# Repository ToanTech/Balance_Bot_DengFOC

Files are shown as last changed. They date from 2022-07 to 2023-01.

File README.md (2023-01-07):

**DengFOC平衡车项目**是基于simplefoc开源的[平衡车项目](https://github.com/simplefoc/Arduino-FOC-balancer)，进行结构改进和效果优化后应用在我开源的[DengFOC](https://gitee.com/link?target=https%3A%2F%2Fgithub.com%2FToanTech%2FDeng-s-foc-controller)双路无刷电机驱动器上的DengFOC配套项目。

balancebot_gif

get_down

**项目完全开源，你可以根据本Github内容自行白嫖，或者，支持一下灯哥的辛勤劳作，进入灯哥开源TB店购买DengFOC平衡车套件，一键配齐。**

[DengFOC 高敏捷自平衡车套件--链接猛击(进店后在 所有宝贝 处可找到)](https://shop564514875.taobao.com/)

# 一、安装过程
## 1.所需元器件

1. DengsFOC V3（你可以在TB搜索灯哥开源进入店铺购买，或根据DengFOC开源仓库的开源资料自制）
1. 2204云台电机*2
1. AS5600编码器*2
1. MPU6050陀螺仪*1
## 2.接线过程
| 零件 | 接线位置 |
| --- | --- |
| 2204云台电机 | DengFoc M0位置 |
| 2204云台电机 | DengFoc M1位置 |
| AS5600 | SDA0,SCL0,3V3,GND |
| AS5600 | SDA1,SCL1,3V3,GND |
| MPU6050 | SDA1,SCL1,3V3,GND |
| 电池以及电源开关线 | DengFoc 电源端子 |

<div align=center>&width=540"</div>
如果你是自行DIY，那么按照上面的接线表格将线接入DengFOC即可；如果你是采用在 [灯哥开源 淘宝店](https://gitee.com/link?target=https%3A%2F%2Fshop564514875.taobao.com%2F) 购买的平衡车套件，那么你会得到**如下所示配套线材**。
配套接线材料：

- AS5600编码器接线套装 一头是杜邦端子，接有一根黑线GND，一根红线VCC，一根绿线SDA，一根黄线SCL，另一端是4p端子。

<div align=center>&width=324"</div>

- MPU6050接线端子套装  两头是4p端子，接有一根黑线GND，一根红线VCC，一根绿线SDA，一根黄线SCL。

<div align=center>&width=217"
</div>

- 电源接线开关
## 3.组装步骤

- AS5600编码器红色线代表VCC，黑色线代表GND，黄线代表SCL，绿色代表SDA。将端子一端的4p端子连接到AS5600对应的端子上。同时将接线端子的另外一端杜邦壳接到DengFoc的排针对应的接口上。

<div align=center>&width=1024"</div>

- MPU6050陀螺仪接线端子红色线代表VCC，黑色线代表GND，黄色线代表SCL，绿色线代表SDA，接线端子一端MPU6050连接，一端与AS5600编码器相连。

<div align=center>&width=1156"</div>

- 电机1三线连接到DengFoc M0端旋转方向为cw，电机2连接到DengFoc M1端旋转方向为ccw。可通过串口查看旋转方向信息，若旋转方向不对可更换电机三相中任意两相顺序。

详细安装过程可以观看安装视频，视频中有关于车体各部分的详细安装步骤以及连线步骤。
<div align=center>&width=951"</div>
# 二、调试过程

- 烧写平衡车代码例程，上电之后等待陀螺仪校准，以及电机校准。
- 看平衡车是否能够自稳。
- 微信扫描下图二维码，进入小程序。

<div align=center>&width=206.4"</div>

- 进入小程序页面，看蓝牙是否连接成功。小程序页面图如下所示。

<div align=center>&width=320"</div>

- 接着移动摇杆看功能是否正常。
- 如果想自己DIY小车控制速度，可以在例程中对小车控制参数进行修改。

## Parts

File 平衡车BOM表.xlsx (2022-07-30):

电控 |  |  | 机械
零件名称 | 数量 | 备注 | 零件名称 | 数量
DengFOC | 1 |  | 车身主体打印件1 | 1
MPU6050 | 1 |  | 车轮打印件 | 2
AS5600 | 2 |  | 车身前盖打印件 | 1
配套传感器径向磁铁 | 2 |  | 车轮轴体打印件2 | 2
2204云台电机 | 2 |  | 编码器支架 | 2
MPU6050 4p端子线 | 2 |  | M2.5*4螺丝 | 8
AS5600 4p端子线 | 2 | 电机TB地址：https://item.taobao.com/item.htm?id=647180650088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 | M3x10螺丝 | 26
3S电池 | 1 |  | M3螺母 | 2

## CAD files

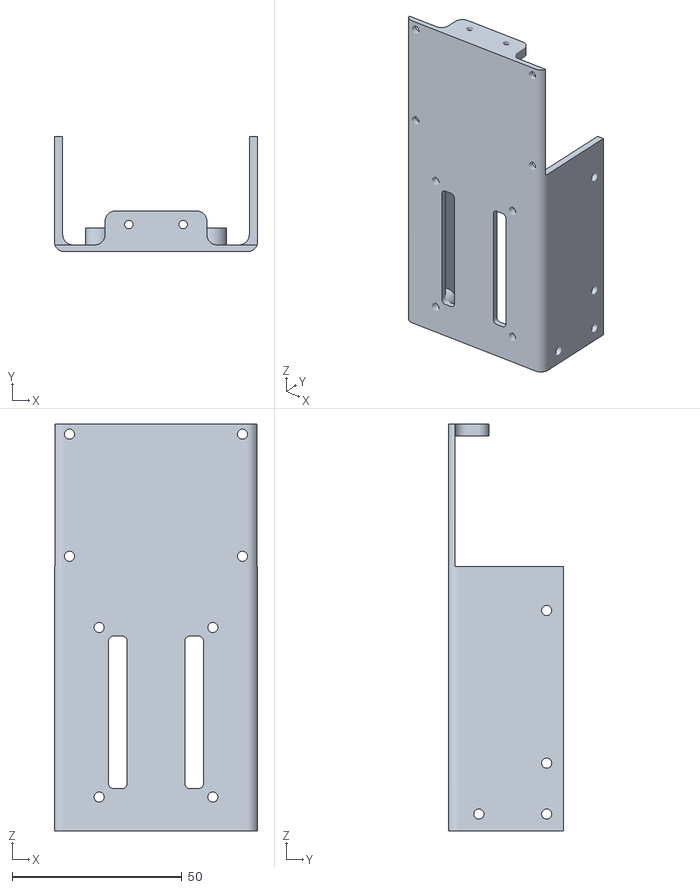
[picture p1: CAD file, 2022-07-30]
平衡车3D打印件/body_21.stl
60.0 x 34.0 x 120.0

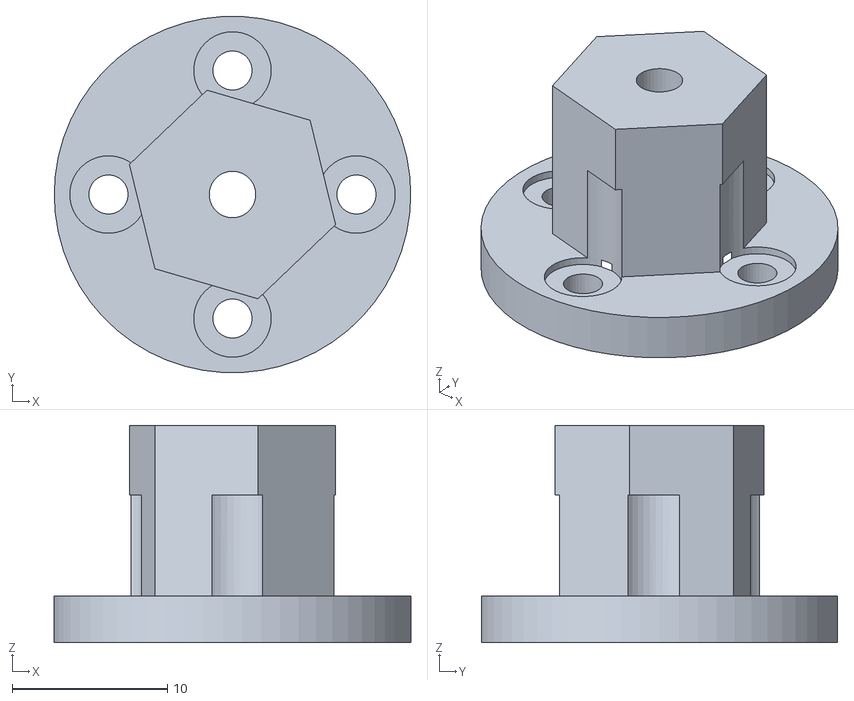
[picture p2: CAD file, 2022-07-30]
平衡车3D打印件/tire_motor_binderx2.STL
23.0 x 23.0 x 14.0

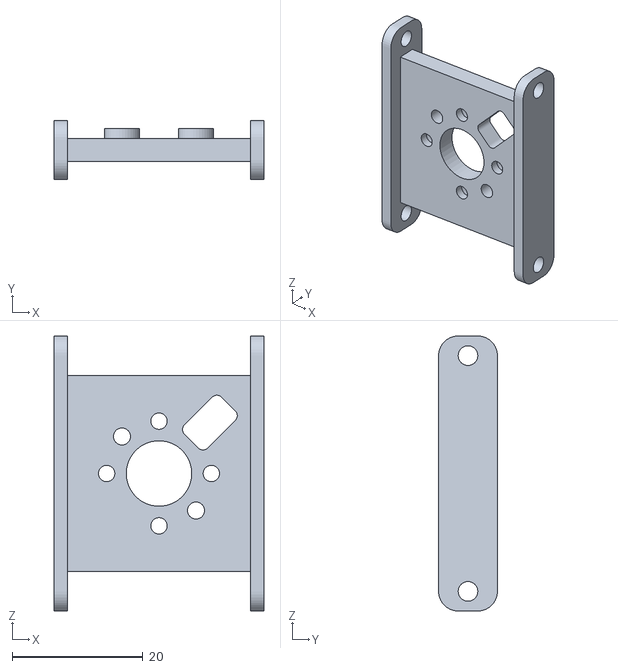
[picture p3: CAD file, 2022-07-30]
平衡车3D打印件/new_car_codex2.STL
32.0 x 9.00 x 42.0

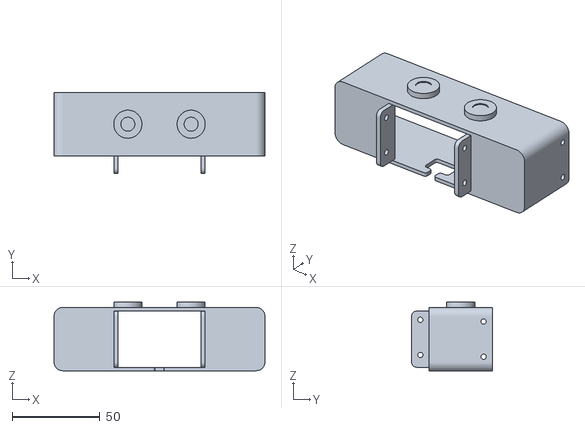
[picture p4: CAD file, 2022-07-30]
平衡车3D打印件/head_19.stl
120.0 x 46.0 x 39.0

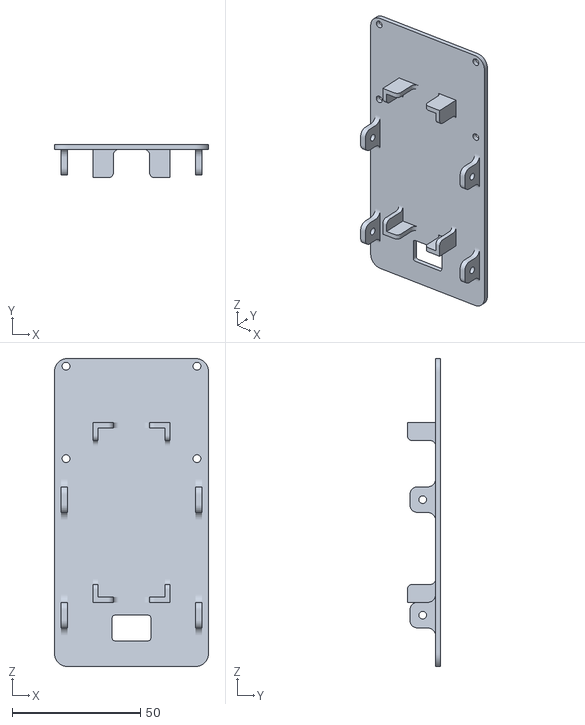
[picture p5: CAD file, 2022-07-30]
平衡车3D打印件/body_cover_with_bat.stl
60.0 x 13.0 x 120.0

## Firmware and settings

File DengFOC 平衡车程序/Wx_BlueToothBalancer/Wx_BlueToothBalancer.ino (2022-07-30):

// 更换蓝牙库
#include <Arduino.h>
#include <SimpleFOC.h>
#include <MPU6050_tockn.h>
#include <BLEDevice.h>
#include <BLEServer.h>
#include <BLEUtils.h>
#include <BLE2902.h>

#define gyroY_OFF -0.56

// 蓝牙参数
BLEServer *pServer = NULL;
BLECharacteristic * pTxCharacteristic;
bool deviceConnected = false;
bool oldDeviceConnected = false;
uint8_t txValue = 0;

#define SERVICE_UUID           "6E400001-B5A3-F393-E0A9-E50E24DCCA9E" // UART service UUID
#define CHARACTERISTIC_UUID_RX "6E400002-B5A3-F393-E0A9-E50E24DCCA9E"
#define CHARACTERISTIC_UUID_TX "6E400003-B5A3-F393-E0A9-E50E24DCCA9E"

TwoWire I2Cone = TwoWire(0);
TwoWire I2Ctwo = TwoWire(1);
MagneticSensorI2C sensor0 = MagneticSensorI2C(AS5600_I2C);
MagneticSensorI2C sensor1 = MagneticSensorI2C(AS5600_I2C);


double acc2rotation(double x, double z);//for kalman
MPU6050 mpu6050(I2Ctwo);


BLDCMotor motor0 = BLDCMotor(7);
BLDCDriver3PWM driver0 = BLDCDriver3PWM(32,33,25,22);

BLDCMotor motor1 = BLDCMotor(7);
BLDCDriver3PWM driver1  = BLDCDriver3PWM(26,27,14,12);

// control algorithm parametersw
// stabilisation pid 自稳PID
//P0.55 I5.5 初始值0.5 5 
PIDController pid_stb{.P = 0.8, .I = 5.5, .D = 0, .ramp = 100000, .limit = 8}; 
// velocity pid 速度PID P初始值1.5
PIDController pid_vel{.P = 1.5, .I = 0, .D = 0.01, .ramp = 10000, .limit = _PI/4};
// velocity control filtering 速度控制滤波，滤波时间常数为0.07
LowPassFilter lpf_pitch_cmd{.Tf = 0.07};
// low pass filters for user commands - throttle and steering 油门和转向滤波
LowPassFilter lpf_throttle{.Tf = 0.5}; //初始值0.5
LowPassFilter lpf_steering{.Tf = 0.1};//初始值0.1

String resStr;
String chipId;
String readString;

float steering = 0;
float throttle = 0;
float new_steering;
float new_throttle;
// max_throttle数值可能需要更改
float max_throttle = 50; // 初始值20 rad/s 
float max_steering = 0.8; //  1V
float Offset_parameters = -9.3; //偏置参数
int Checkcomma; //判断是否含有逗号分隔


Commander commander = Commander(Serial);
void cntStab(char* cmd) {  commander.pid(&pid_stb, cmd);}
void cntMove(char* cmd) {  commander.pid(&pid_vel, cmd);}
void lpfPitch(char* cmd) {  commander.lpf(&lpf_pitch_cmd, cmd);}
void lpfSteering(char* cmd) {  commander.lpf(&lpf_steering, cmd);}
void lpfThrottle(char* cmd) {  commander.lpf(&lpf_throttle, cmd);}

class MyServerCallbacks: public BLEServerCallbacks {
    void onConnect(BLEServer* pServer) {
      deviceConnected = true;
    };

    void onDisconnect(BLEServer* pServer) {
      deviceConnected = false;
    }
};



class MyCallbacks: public BLECharacteristicCallbacks {
    void onWrite(BLECharacteristic *pCharacteristic) {
      std::string rxValue = pCharacteristic->getValue();

      if (rxValue.length() > 0) {
        Serial.print("Received Value: ");
        // 打印蓝牙接收信息
        for (int i = 0; i < rxValue.length(); i++){
//          Serial.print(rxValue[i]);
          resStr += rxValue[i];
        }
        Checkcomma = resStr.indexOf(',');
        if(Checkcomma != -1){
          new_steering = resStr.substring(0,Checkcomma).toInt();
          new_throttle = resStr.substring(Checkcomma+1,resStr.length()).toInt();
          steering = max_steering * new_steering/50;
          throttle = max_throttle * -new_throttle/50;
//          Serial.print("new_steering:");
//          Serial.print(new_steering);
//          Serial.print("\t");
//          Serial.print("new_throttle:");
//          Serial.print(new_throttle);
//          Serial.print("Y:");
//          Serial.print(throttle);
//          Serial.print("\t");
//          Serial.print("X:");
//          Serial.println(steering);
        }
        else{
          steering = 0;
          throttle = 0;
        }
        // 清空数据准备下次接收
        resStr = "";
      }
    }
};

void setup(){
    Serial.begin(115200);
    _delay(750);

    chipId = String((uint32_t)ESP.getEfuseMac(), HEX);
    chipId.toUpperCase();
    Serial.println(chipId);
    //  初始化蓝牙 蓝牙名称
    BLEDevice::init("Blue Control");

    // 开启一个蓝牙服务
    pServer = BLEDevice::createServer();
    pServer->setCallbacks(new MyServerCallbacks());

    BLEService *pService = pServer->createService(SERVICE_UUID);

    pTxCharacteristic = pService->createCharacteristic(
                        CHARACTERISTIC_UUID_TX,
                        BLECharacteristic::PROPERTY_NOTIFY
                      );

    pTxCharacteristic->addDescriptor(new BLE2902());

    BLECharacteristic * pRxCharacteristic = pService->createCharacteristic(
        CHARACTERISTIC_UUID_RX,
        BLECharacteristic::PROPERTY_WRITE
                                          );

    pRxCharacteristic->setCallbacks(new MyCallbacks());

    pService->start();

    pServer->getAdvertising()->start();
    Serial.println("Waiting a client connection to notify...");

    I2Cone.begin(19,18, 400000UL); 
    I2Ctwo.begin(23,5, 400000UL);
  
    sensor0.init(&I2Cone);
    sensor1.init(&I2Ctwo);

    mpu6050.begin();
    mpu6050.calcGyroOffsets(true);

    // link the motor to the sensor
    motor0.linkSensor(&sensor0);
    motor1.linkSensor(&sensor1);

     // 速度环PID参数
    motor1.PID_velocity.P = 0.05;
    motor1.PID_velocity.I = 1;
    motor1.PID_velocity.D = 0;

    motor0.PID_velocity.P = 0.05;
    motor0.PID_velocity.I = 1;
    motor0.PID_velocity.D = 0;

    motor0.voltage_sensor_align = 6;
    driver0.voltage_power_supply = 8;
    driver0.init();
    motor0.linkDriver(&driver0);
    motor1.voltage_sensor_align = 6;
    driver1.voltage_power_supply = 8;
    driver1.init();
    motor1.linkDriver(&driver1);

    motor0.torque_controller = TorqueControlType::voltage;
    motor1.torque_controller = TorqueControlType::voltage;
    motor0.controller = MotionControlType::torque;
    motor1.controller = MotionControlType::torque;

    // enable monitoring
    motor1.useMonitoring(Serial);
    motor0.useMonitoring(Serial);

    // initialise motor
    motor1.init();
    motor0.init();
    // align encoder and start FOC
    motor1.initFOC();
    motor0.initFOC();

    commander.add('A', cntStab, "pid stab");
    commander.add('B', cntMove, "pid vel");
    commander.add('C', lpfThrottle, "lpf vel command");
    commander.add('D', lpfPitch, "lpf throttle");
    commander.add('E', lpfSteering, "lpf steering");

}

void loop(){
    while (Serial.available() > 0) {
    if (deviceConnected) {
      delay(3);
      readString += Serial.read();
      pTxCharacteristic->setValue(chipId.c_str());
      pTxCharacteristic->notify();
      Serial.println(chipId);

    }
  }
    // 未连接
    if (!deviceConnected && oldDeviceConnected) {
    delay(500); 
    pServer->startAdvertising(); // restart advertising
    Serial.println("start advertising");
    oldDeviceConnected = deviceConnected;
    }
  // 连接成功
    if (deviceConnected && !oldDeviceConnected) {
    oldDeviceConnected = deviceConnected;
    }
    motor1.loopFOC();
    motor0.loopFOC();
    motor1.move();
    motor0.move();

    mpu6050.update();
    double mpu_pitch = mpu6050.getAngleY();// tockn的getangle，通过一阶置信计算
    float target_pitch = lpf_pitch_cmd(pid_vel((motor0.shaft_velocity + motor1.shaft_velocity) / 2 - lpf_throttle(throttle)));
//    Serial.println(target_pitch);
    float voltage_control = pid_stb(Offset_parameters - mpu_pitch + target_pitch);
    float steering_adj = lpf_steering(steering);
  
    motor0.target = voltage_control - steering_adj;
    motor1.target = voltage_control + steering_adj;
    commander.run();

}
